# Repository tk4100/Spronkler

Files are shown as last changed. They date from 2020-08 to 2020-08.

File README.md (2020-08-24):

# Spronkler
A sprinkler controller for raspberry pi, python controller software and KiCAD PCB design files.  Please please please don't edit
the "as-ordered" PCB files, for reasons that should be obvious.  They're useful for debugging boards of a particular revision.

# Software Architecture
Two main pieces, the webterface and the controller daemon.  The webUI is so far undesigned, but will communicate over ZMQ
to the controller daemon.

The controller daemon code is in Python, a master class with each major task in it's own thread/object, communicating with
inproc ZMQ. One of the aspects I wanted to explore was completely self-contained threads, each thread is responsible for
sanity in its own domain.  No matter what crazy commands are received via the ZMQ interface, a given thread should behave
safely.

## Controller
### Pin Daemon
Pretty simple here, controls actual GPIO outputs, and is responsible for preventing multiple channels from running at
once, as well as enforcing guard intervals etc.

### Schedule Daemon
Handles Schduling, with a total time-awareness of 365 days.  The plan is to have this daemon accept JSON objects
that represent a schedule, compare this new schedule with all other currently active schedules, reject the new
schedule if needed with a helpful message (ie, "conflicts with schedule 9, 'Rosemary dripline").  Similar logic
is required for activating/deactivating schedules.

Example schedule object.  It runs from May 1st, and repeats every 24 hours until October 1st.  The date is recorded in iso
format, but the year will be ignored. Looking at the schedule section, channel 1 runs for 5 minutes, channel 2 for 4 minutes,
and so on.
```json
{
   "name":"Demo Schedule",
   "start_time":"05-01T06:00:00",
   "end_time":"10-01T20:00:00",
   "interval_minutes":1440,
   "enabled":"true",
   "schedule":{
      "1":5,
      "2":4,
      "3":2,
      "4":4,
      "5":4,
      "6":5,
      "7":3,
      "9":5,
      "10":6,
      "12":6
   }
}
```

### API Daemon
The connection point to the webUI.  Probably will start out life as a simple bridge with one inproc ZMQ endpoint, and one
ipc or tcp endpoint.

# Hardware Architecture
A board powered by 24VAC which provides +5V on a standard Raspberry Pi header, as well as 3V3-safe inputs for a set of
opto-isolators.  ATM the power supply is linear, which doesn't work in practice, as it rapidly overheats from dropping
something like 29V.  The next rev will have a switching reg.

Pi Zero = ~125mA.  29 * 0.125 = **3.625W**

3.625W == Wayyy too much to dissipate in this package.  Anything over about 500mW requires a heatsink, and we don't want that.

## PSU
An LM317T and some caps.

***Note:*** There might be a noise problem here too.  I'm assuming the issue with Pi restarts is heat in the LM317, but
we might need some better noise suppression.  Don't forget to check before spinning a new board.

The [LMZ14201HTZ](https://www.digikey.com/product-detail/en/texas-instruments/LMZ14201HTZ-NOPB/LMZ14201HTZ-NOPBCT-ND/2533811) is
pricey, but appeals to my laziness.

# I/O
An opto-isolated SSR across common and each sprinkler channel.  Only a TVS diode is protecting the AC side of these, which
may not be right.  A FET with a pullup controls the inputs here, which are in series with LED indication on the board.

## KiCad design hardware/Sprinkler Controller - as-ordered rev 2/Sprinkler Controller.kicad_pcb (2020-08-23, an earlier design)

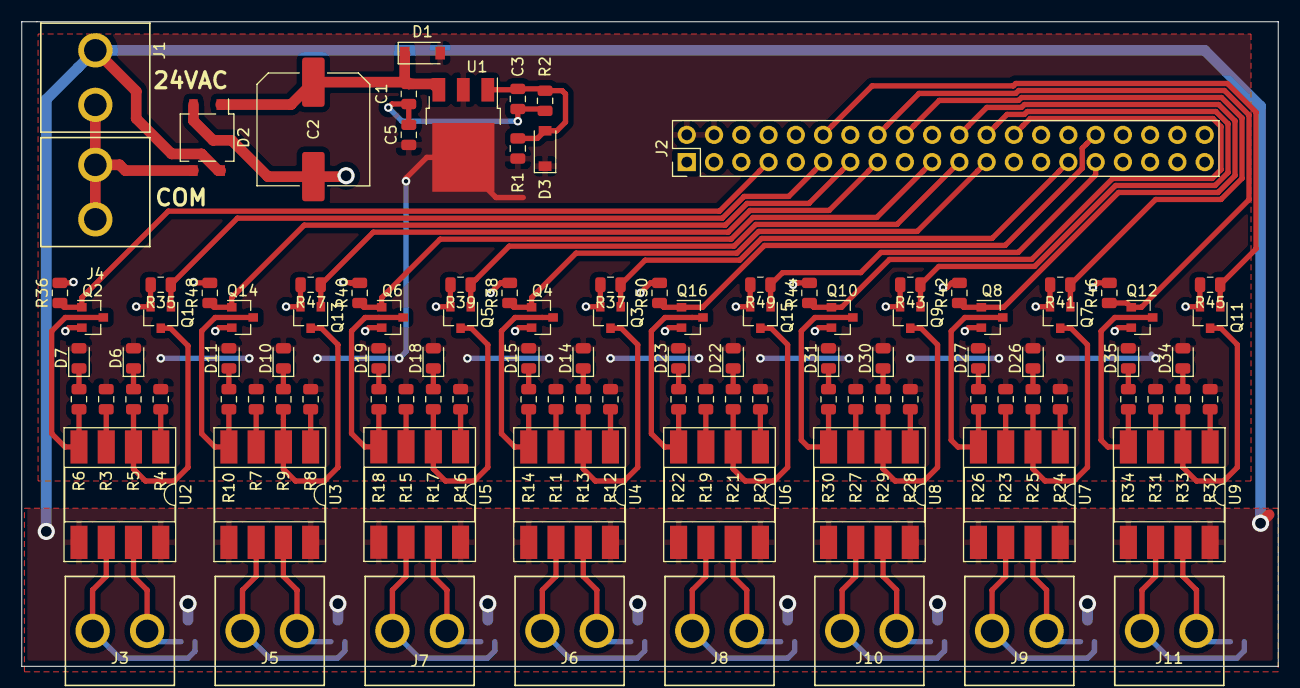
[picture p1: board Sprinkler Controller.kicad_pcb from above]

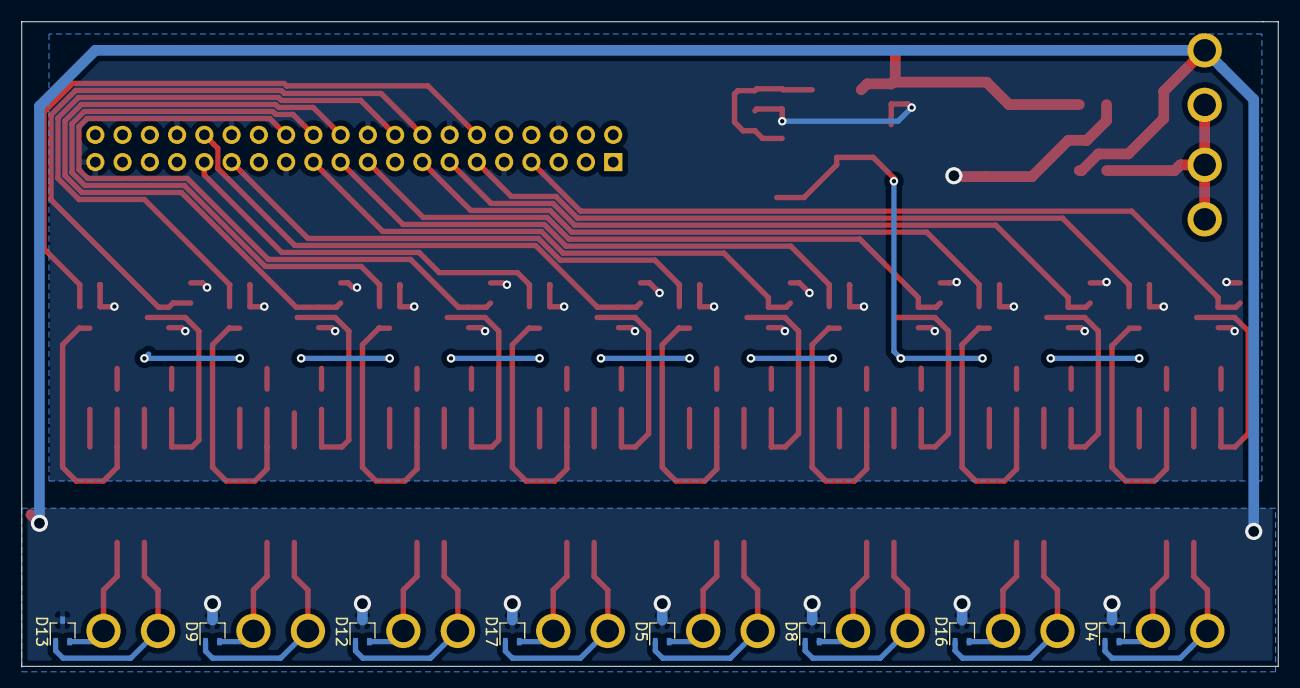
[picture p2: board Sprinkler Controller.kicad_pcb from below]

Board: 2 copper layers, 117.1 x 60.1 mm, 117 parts (8 on the bottom side), 86 nets.

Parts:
C1: 0.1u; C_0805_2012Metric
C2: 220u; C_Elec_10x10.2
C3, C5: 1u; C_0805_2012Metric
D1, D3: D_Small; D_SOD-123
D2: D_Bridge_+-AA; TO-269AA
D4, D5, D8, D9, D12, D13, D16, D17: PESD1CAN-U; SOT-323_SC-70
D6, D7, D10, D11, D14, D15, D18, D19, D22, D23, D26, D27, D30, D31, D34, D35: LED_Small; LED_0805_2012Metric
J1, J3, J4, J5, J6, J7, J8, J9, J10, J11: Conn_01x02; Terminal_2P_5mm
J2: Conn_02x20_Odd_Even; PinHeader_2x20_P2.54mm_Vertical
Q1, Q2, Q3, Q4, Q5, Q6, Q7, Q8, Q9, Q10, Q11, Q12, Q13, Q14, Q15, Q16: Q_NMOS_GSD; SOT-23
R1: 4K7; R_0805_2012Metric
R2: 14K; R_0805_2012Metric
R3, R4, R7, R8, R11, R12, R15, R16, R19, R20, R23, R24, R27, R28, R31, R32: 680R; R_0805_2012Metric
R5, R6, R9, R10, R13, R14, R17, R18, R21, R22, R25, R26, R29, R30, R33, R34: 2K; R_0805_2012Metric
R35, R36, R37, R38, R39, R40, R41, R42, R43, R44, R45, R46, R47, R48, R49, R50: 10K; R_0805_2012Metric
U1: LM317_3PinPackage; TO-252-3_TabPin2
U2, U3, U4, U5, U6, U7, U8, U9: G3VM-62F1; DIP-8_W8.89mm_SMDSocket_LongPads

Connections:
+5V: C5.1, D1.2, D3.1, D6.2, D7.2, D10.2, D11.2, D14.2, D15.2, D18.2, D19.2, D22.2, D23.2, D26.2, D27.2, D30.2, D31.2, D34.2, D35.2, J2.2, J2.4, R1.1, R3.2, R4.2, R7.2, R8.2, R11.2, R12.2, R15.2, R16.2, R19.2, R20.2, R23.2, R24.2, R27.2, R28.2, R31.2, R32.2, U1.2
+VDC: C1.1, C2.1, D1.1, D2.1, U1.3
/Channel_1: J2.11, Q1.1, R35.1
/Channel_2: J2.7, Q2.1, R36.1
/Channel_3: J2.15, Q13.1, R47.1
/Channel_4: J2.13, Q14.1, R48.1
/Channel_5: J2.21, Q5.1, R39.1
/Channel_6: J2.19, Q6.1, R40.1
/Channel_7: J2.29, Q3.1, R37.1
/Channel_8: J2.23, Q4.1, R38.1
/Channel_9: J2.16, Q12.1, R46.1
/Channel_10: J2.12, Q11.1, R45.1
/Channel_11: J2.26, Q10.1, R44.1
/Channel_12: J2.24, Q9.1, R43.1
/Channel_13: J2.32, Q16.1, R50.1
/Channel_15: J2.22, Q8.1, R42.1
/Channel_16: J2.18, Q7.1, R41.1
/sheet5ED885F3/C_1: J2.31, Q15.1, R49.1
GND: C1.2, C2.2, C3.2, C5.2, D2.2, J2.6, J2.9, J2.14, J2.20, J2.25, J2.30, J2.34, J2.39, Q1.2, Q2.2, Q3.2, Q4.2, Q5.2, Q6.2, Q7.2, Q8.2, Q9.2, Q10.2, Q11.2, Q12.2, Q13.2, Q14.2, Q15.2, Q16.2, R2.2, R35.2, R36.2, R37.2, R38.2, R39.2, R40.2, R41.2, R42.2, R43.2, R44.2, R45.2, R46.2, R47.2, R48.2, R49.2, R50.2
unnamed: C3.1, D3.2, R1.2, R2.1, U1.1
unnamed: D4.1, J3.2, U2.6
unnamed: D4.2, J3.1, U2.7
unnamed: D5.1, J6.2, U4.6
unnamed: D5.2, J6.1, U4.7
unnamed: D6.1, R5.1
unnamed: D7.1, R6.1
unnamed: D8.1, J7.2, U5.6
unnamed: D8.2, J7.1, U5.7
unnamed: D9.1, J9.2, U7.6
unnamed: D9.2, J9.1, U7.7
unnamed: D10.1, R9.1
unnamed: D11.1, R10.1
unnamed: D12.1, J10.2, U8.6
unnamed: D12.2, J10.1, U8.7
unnamed: D13.1, J11.2, U9.6
unnamed: D13.2, J11.1, U9.7
unnamed: D14.1, R13.1
unnamed: D15.1, R14.1
unnamed: D16.1, J5.2, U3.6
unnamed: D16.2, J5.1, U3.7
unnamed: D17.1, J8.2, U6.6
unnamed: D17.2, J8.1, U6.7
unnamed: D18.1, R17.1
unnamed: D19.1, R18.1
unnamed: D22.1, R21.1
unnamed: D23.1, R22.1
unnamed: D26.1, R25.1
unnamed: D27.1, R26.1
unnamed: D30.1, R29.1
unnamed: D31.1, R30.1
unnamed: D34.1, R33.1
unnamed: D35.1, R34.1
unnamed: Q1.3, R5.2, U2.2
unnamed: Q2.3, R6.2, U2.4
unnamed: Q3.3, R13.2, U4.2
unnamed: Q4.3, R14.2, U4.4
unnamed: Q5.3, R17.2, U5.2
unnamed: Q6.3, R18.2, U5.4
unnamed: Q7.3, R25.2, U7.2
unnamed: Q8.3, R26.2, U7.4
unnamed: Q9.3, R29.2, U8.2
unnamed: Q10.3, R30.2, U8.4
unnamed: Q11.3, R33.2, U9.2
unnamed: Q12.3, R34.2, U9.4
unnamed: Q13.3, R9.2, U3.2
unnamed: Q14.3, R10.2, U3.4
unnamed: Q15.3, R21.2, U6.2
unnamed: Q16.3, R22.2, U6.4
unnamed: R3.1, U2.3
unnamed: R4.1, U2.1
unnamed: R7.1, U3.3
unnamed: R8.1, U3.1
unnamed: R11.1, U4.3
unnamed: R12.1, U4.1
unnamed: R15.1, U5.3
unnamed: R16.1, U5.1
unnamed: R19.1, U6.3
unnamed: R20.1, U6.1
unnamed: R23.1, U7.3
unnamed: R24.1, U7.1
unnamed: R27.1, U8.3
unnamed: R28.1, U8.1
unnamed: R31.1, U9.3
unnamed: R32.1, U9.1
VAC+: D2.3, J1.1, J4.1, J4.2
VAC-: D2.4, D4.3, D5.3, D8.3, D9.3, D12.3, D13.3, D16.3, D17.3, J1.2, U2.5, U2.8, U3.5, U3.8, U4.5, U4.8, U5.5, U5.8, U6.5, U6.8, U7.5, U7.8, U8.5, U8.8, U9.5, U9.8

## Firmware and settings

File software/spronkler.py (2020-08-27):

#!/usr/bin/env python3
import time
import datetime
import pytz
import json
import threading
import zmq

# using the LED function to handle our pins.  It's a LED in an opto-isolator, after all : D
from gpiozero import LED


# Spronkler
class Spronkler():
    def __init__(self, pinmap):

        # set up ZMQ and start threads
        self.zmqctx = zmq.Context()
        
        # set up the daemons
        self.pinDaemon = self.PinDaemon(self.zmqctx, pinmap)
        self.scheduleDaemon = self.ScheduleDaemon(self.zmqctx)
        
        self.scheduleDaemon.pinDaemonZMQ = self.pinDaemon.zmq_address

        # wait for the threads to be ready
        pinDaemonAlive = False
        scheduleDaemonAlive = False
        while pinDaemonAlive == False or scheduleDaemonAlive == False:
            try:
                pinDaemonAlive = self.pinDaemon.ping()
                scheduleDaemonAlive = self.scheduleDaemon.ping()
            except zmq.error.Again:
                print("Daemons not yet alive....")
                continue

            time.sleep(0.25)

    # daemon-generic stuff
    class Daemon():
        class MsgPing():
            pass

        class MsgPong():
            pass

        class MsgNAK():
            def __init__(self, reason):
                self.reason = reason

        class MsgACK():
            def __init__(self, reason=""):
                self.reason = reason

        def ping(self):
            sock = self.zmqctx.socket(zmq.REQ)
            sock.setsockopt(zmq.RCVTIMEO, 250)
            sock.connect(self.zmq_address)

            msg = self.MsgPing()

            sock.send_pyobj(msg)
            msg = sock.recv_pyobj()

            if type(msg) == type(self.MsgPong()):
                self.log("Pinged succesfully.")
                retcode = True
            else:
                self.log("Non-ACK response received: {}.".format(type(msg)))
                retcode = False

            sock.close()
            return(retcode)
            
        def log(self, message):
            try:
                with open("logs/{}.log".format(self.threadname), "a") as logh:
                    message = "[{}]: {}\n".format(datetime.datetime.now(), message)
                    logh.write(message)
            except Exception as e:
                print("FAILED TO LOG MESSAGE!  Too bad you won't see this when I'm a daemon :(  ({})".format(str(e)))


    # Pin Controller Daemon
    class PinDaemon(Daemon):

        class MsgEnable():
            def __init__(self, pinmap):
                self.pinmap = pinmap

        class MsgDisable():
            pass

        class MsgSetChan():
            def __init__(self, channel, state):
                self.channel = channel
                self.state = state

        def __init__(self, ctx, pinmap):
            # ZMQ setup
            self.threadname = "pinDaemon"
            self.zmqctx = ctx
            self.zmq_address = "inproc://pinDaemon"
            self.__daemonThread = threading.Thread(name=self.threadname, target=self.__daemonThread)
            self.max_active_channels = 1

            #start the thread
            self.__daemonThread.start()

            #init
            self.init(pinmap)

        # Daemon thread
        def __daemonThread(self):
            # zmq connect
            sock = self.zmqctx.socket(zmq.REP)
            sock.bind(self.zmq_address)

            # track the number of active channels, and the time of last state change for each pin
            on_count = 0
            last_state_change = {}
            controller_state = ''

            while True:
                msg = sock.recv_pyobj()
                # switch on relevant message types
                # ping
                if isinstance(msg, self.MsgPing):
                    self.log("Received ping")
                    msg = self.MsgPong()

                # set channel
                elif isinstance(msg, self.MsgSetChan):
                    # bounce the request if we're not yet enabled
                    if controller_state != "ENABLED":
                        msg = self.MsgNAK("Controller not enabled.")

                    # convert any string channels to ints, warning as we do so.
                    if type(msg.channel) == type("this is a string"):
                        self.log("Received a string channel number, converting to int and subtracting one.  Fix your code!")
                        msg.channel = int(msg.channel) - 1

                    # set a channel
                    try:
                        if msg.state == True and on_count < self.max_active_channels:
                            CHANNELS[msg.channel].on()
                            self.log("Channel {} ON.".format(msg.channel))
                            on_count += 1
                            msg = self.MsgACK()
                        elif msg.state == True and on_count >= self.max_active_channels:
                            msg = self.MsgNAK("Too many channels already active!")
                        elif msg.state == False:
                            CHANNELS[msg.channel].off()
                            self.log("Channel {} OFF.".format(msg.channel))
                            on_count -= 1
                            msg = self.MsgACK()
                    except IndexError:
                        msg = self.MsgNAK("Channel {} does not exist!".format(msg.channel))
                    except Exception as e:
                        msg = self.MsgNAK("Exception occurred! {}".format(str(e)))

                # emable/set pinmap
                elif isinstance(msg, self.MsgEnable):
                    if controller_state == "ENABLED":
                        msg = self.MsgNAK("Controller already enabled.")
                    # update internals
                    PINMAP = msg.pinmap
                    CHANNELS = []
                    controller_state = "ENABLED"

                    for pin in PINMAP:
                        CHANNELS.append(LED(pin))
                        CHANNELS[-1].off()

                    self.log("Output enabled, with pinmap '{}'".format(', '.join( [ str(x) for x in msg.pinmap ] )))
                    msg = self.MsgACK()
                
                # disable all outputs
                elif isinstance(msg, self.MsgDisable):

                    # update internals
                    for chan in CHANNELS:
                        chan.off()

                    while len(CHANNELS) > 0:
                        del(CHANNELS[-1])
                    
                    self.log("All outputs set low and disabled!")
                    msg = self.MsgACK()

                # Fallthrough
                else:
                    msg = self.MsgNAK("Unknown Message")

                # reply
                sock.send_pyobj(msg)

        # enable the pin daemon and set the pin mappings
        def init(self, pinmap):
            sock = self.zmqctx.socket(zmq.REQ)
            sock.connect(self.zmq_address)
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

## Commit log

2020-08-23 Add in all the hardware stuff
    [Sprinkler Controller.kicad_pcb, Sprinkler Controller.sch, indication.sch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]
2020-08-23 tracking double schedule issue
    [spronkler.py]
2020-08-23 add a print call i forgot
2020-08-24 change log path, fix tabs, remove redundant thread naming in named logs.
    [spronkler.py]
2020-08-24 Fix typo Add new constantly-running schedule Add check for schedules that self-interfere, ie they start more frequently than they can complete a cycle.
    [spronkler.py]
2020-08-24 actually pass args to the schedule runner thread
2020-08-25 push entire schedule to runner thread
2020-08-25 Reset a schedule's running status after interval_minutes have passed since start. Doesn't reap old runner threads.
    [spronkler.py]
2020-08-25 This version is broken, see the note on line 407
    [spronkler.py]
2020-08-26 lotsa prints
2020-08-27 try using 2000 instead of 1900 to avoid platform time_t issues
    [spronkler.py]
